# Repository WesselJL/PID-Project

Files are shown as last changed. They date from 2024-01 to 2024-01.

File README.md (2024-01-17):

# PID-Project
PID ball balanceer project 

Het PID bal balanceer project is een project waarbij een balletje wordt gebalanceerd in een goot door middel van een proportioneel-integraal-differentiaal regelaar. De hardware van het project bevat een ESP32 WROOM, VL530IX time of flight sensor en een servo motor. Deze elektro componenten zijn geinstalleerd op een 3D geprinte opstelling die ontworpen is (zie afbeelding van de opstelling hieronder).

WhatsApp Image 2024-01-15 at 14 33 00

## **Uitleg ontwerpkeuzes 3D print**

Het ontwerp van de 3D modellen is zo simpel mogelijk gemaakt. Het gehele model is opgedeeld in 4 delen zodat het op elke gemiddelde 3D printer geprint kan worden en zodat wanneer een onderdeel vervangen of opnieuw ontworpen moet worden het per deel gedaan kan worden. Het ontwerp bestaat uit een goot/ balk waar een balletje in kan rollen. Deze goot/ balk kan in elkaar worden geschoven en wordt bij elkaar gehouden door het middelste kantelpunt waar een bout door heen zit. Naast het middelste kantelpunt is er nog een ander kantelpunt, dit kantelpunt is het punt waar de servo motor de goot/ balk mee laat bewegen.

Op de 3D geprinte delen zijn bevestigings punten voor zowel de servo motor als de time of flight sensor. Deze motor en sensor zijn vastgemaakt met standaard maat boutjes en moeren. Het vierde en laaste deel van het model is de voetsteun. Deze steun zit vast aan het middelste kantelpunt, het kantelpunt van de servo motor en de servo motor zelf zitten ook vast aan deze voetsteun. 

> [!TIP]
> Zorg er voor dat de bouten van de kantelpunten niet te groot zijn, dit maakt het voor de servo motor moeilijk om te bewegen/ de bal te kantelen.

## **Uitleg Componentkeuze**

Voor dit PID bal balanceer project is er gekozen voor de MG90-servo, de VL53L0X ToF-sensor en de ESP32 WROOM. Deze keuzes zijn gebaseerd op de eigenschappen en functionaliteiten van elk component, deze eigenschappen en functionaliteit zorgen ervoor dat de bal gebalanceerd kan worden door middel van de gecodeerde PID regelaar.

### *MG90 Servo*

MG90S-180-1

De MG90-servo is gekozen vanwege de volgende eigenschappen: nauwkeurig, betrouwbaar, betaalbaar en relatief klein. Met een hoog koppel voor de afmeting van de servo motor en de nauwkeurig stapgrootte maakt de MG90 het moeglijk om de bal precies en snel te balanceren. Bovendien is het compacte formaat van de servo gunstig voor het toepassen in ons project, hierdoor is het te printen onderdeel compact te houden.

### *VL530IX tof sensor*

550x332

De VL53L0X Time-of-Flight-sensor is een belangrijk component in dit project vanwege de mogelijkheid om snel en nauwkeurig afstanden te meten. Het ToF-principe zorgt er voor dat in real-time de afstands gegevens worden verkregen over de afstand tussen de sensor en de bal die gebalanceerd moet worden. Deze gegevens zijn essentieel voor de PID-regeling om snel en effectief te reageren op veranderingen in de positie van de bal. Deze sensor kan afstanden meten tot 2 meter dus dat is ruim voldoende voor deze opstelling. De snelste modus van de sensor kan met een afstand van 1.2 meter en een nauwkeurigheid van +/- 5% elke 20ms een afstand meten. 

### *ESP32 WROOM*

61o2ZUzB4XL _AC_UF894,1000_QL80_

De keuze voor de ESP32 WROOM als microcontroller is gemaakt omdat die een krachtige processor, wifi mogelijkheid en brede ondersteuning in de open source wereld heeft. De dual-core processor op 240 MHz biedt voldoende rekenkracht om de PID-regeling te implementeren en tegelijkertijd andere taken uit te voeren. Bovendien maakt de geïntegreerde Wi-Fi-connectiviteit van de ESP32 WROOM draadloze communicatie mogelijk, waardoor het gemakkelijk is om gegevens PID waardes live aan te kunnnen passen. Dit is een leuke ADD-on voor interactieve lessen voor studenten. 

> [!NOTE]
> De componenten die hierboven genoemd en toegelicht zijn zitten aangesloten op een gaatjes print. De kabels dienen lang genoeg te zijn, dit omdat de sensor met de balk/ goot mee kantelt wanneer de bal gebalanceerd wordt.

## **Uitleg Code**

De code voor dit bal balanceer project d.m.v. PID is gestart door eerst een systeem te maken wat de bal kon balanceren met de sensor waardes die de tof sensor als output gaf zonder PID. Toen de bal succesvol gebalanceerd werd is de PID regeling geprogrammeerd en getest. De uitleg van de 2 programma's en de PID berekeningen staat hieronder.

### *Code zonder PID*

Dit onderstaande gedeelte is het toevoegen van de gebruikte libaries. Zoals de comments het al zeggen zijn het de libaries voor de I2C communicatie, time of flight sensor en de servo motor.

```ruby
#include <Wire.h> // libary voor I2C-communicatie
#include <Adafruit_VL53L0X.h> // VL53L0X sensor libary 
#include <ESP32Servo.h> // libary voor Servo motor
```
Dan als volgende is het de pin initialisatie van de servo motor, initialisatie van de VL53LOX variabele en de servo variabele.

```ruby
#define SERVO_PIN 12 // Definitie van de pin (PIN 12) voor de uitvoer van de aansturing van de Servo-motor
Adafruit_VL53L0X lox = Adafruit_VL53L0X(); // Initialisatie van de sensor variabele
Servo servo; // Initialisatie van de Servo motor
```
In de setup van het programma wordt de seriële communicatie opgesteld en wordt er gecontroleerd of de VL53LOX juist is opgestart. Wanneer dit niet het geval is dan wordt er een foutmelding in de seriële monitor geprint en blijft het systeem in een oneindige 'halt' loop. Daarnaast wordt ook de servo variabele gekoppeld aan de Servo pin en wordt de positie van de servo motor ingesteld op 90 graden, dit is de start positie.

```ruby
void setup() {
  Serial.begin(115200); // Initialisatie van de seriële communicatie met een baudrate van 115200 bps
  Serial.println("Ping Pong Ball Balancing"); // Uitvoer van een start bericht

  if (!lox.begin()) { // Controle op het starten van de VL53L0X-sensor
    Serial.println(F("Failed to boot VL53L0X")); // Uitvoer van een foutmelding bij mislukken en stoppen van het programma
    while (1);
  }

  servo.attach(SERVO_PIN); // Koppeling van de Servo variabele aan de gedefinieerde pin
  servo.write(90); // Instellen van de initiële positie van de Servo-motor op 90 graden

  delay(500); // Wachten om de Servo-motor naar de initiële positie te laten bewegen
}
```
In de loop van het programma wordt de afstand tot de bal gemeten door de sensor en wordt er gecontroleerd of deze meting een geldige meting is. Daarna wordt de de minimale sensor waarde en de maximale waarde omgezet naar een servo waarde van 0 tot 180. Dit wordt gedaan met de "map" functie. Vervolgens wordt de variabele "servoPosition" naar de Servo gestuurd. In de volgende [video](https://youtu.be/PQ2CX1DTkAU) kan je zien hoe de bal gebalanceerd wordt zonder PID, 

```ruby
void loop() {
  VL53L0X_RangingMeasurementData_t measure; // Definitie van de bal voor de VL53L0X-sensor
  
  lox.rangingTest(&measure, false); // Uitvoeren van een afstandsmeting met de VL53L0X-sensor

  if (measure.RangeStatus != 4) {  // Controleren of de meting geldig is
    int distance = measure.RangeMilliMeter; // Uitlezen van de gemeten afstand in millimeters
    Serial.print("Distance (mm): "); // Uitvoer van het label "Distance (mm): "
    Serial.println(distance); // Uitvoer van de gemeten afstand
    
    // Aanpassen van de positie van de Servo-motor op basis van de gemeten afstand
    int servoPosition = map(distance, 20, 270, 0, 180); // Aanpassen van de mapping-bereik op basis van de opstelling
    servo.write(servoPosition); // Aansturen van de Servo-motor naar de berekende positie
    
    delay(50); // Aanpassen van deze vertraging om de responsiviteit van het systeem te regelen
  } else {
    Serial.println("Out of range"); // Uitvoer van een melding wanneer de gemeten afstand buiten bereik is
  }
}
```
> [!IMPORTANT]
> De waardes 20 & 270 in de 'int servoPosition = map(distance, 20, 270, 0, 180);' line moeten worden aangepast naar de minimale en maximale sensor waarde van je eigen sensor. Deze zijn te verkrijgen door je object wat gebalanceerd moet worden op zijn positie die het dichtsbij de sensor zit en het verste weg van de sensor zit. Deze zijn uit te lezen door het uitvoeren van onderstaande code:

```ruby
#include <Wire.h> // libary voor I2C-communicatie
#include <Adafruit_VL53L0X.h> // libary voor VL53L0X sensor

Adafruit_VL53L0X lox = Adafruit_VL53L0X(); // Initialisatie van de VL53L0X variabele

void setup() {
  Serial.begin(115200); // Initialisatie van de seriële communicatie met een baudrate van 115200 bps
  Serial.println("Ping Pong Ball Balancing"); // Uitvoer van een begroetingsbericht

  if (!lox.begin()) { // Controle op het starten van de VL53L0X-sensor
    Serial.println(F("Failed to boot VL53L0X")); // Uitvoer van een foutmelding bij mislukken en stoppen van het programma
    while (1);
  }

  delay(500); // Wachten om de sensor op te starten
}

void loop() {
  VL53L0X_RangingMeasurementData_t measure; // Definitie van de bal voor de VL53L0X-sensor
  
  lox.rangingTest(&measure, false); // Uitvoeren van een afstandsmeting met de VL53L0X-sensor

  if (measure.RangeStatus != 4) {  // Controleren of de meting geldig is
    int distance = measure.RangeMilliMeter; // Uitlezen van de gemeten afstand in millimeters
    Serial.print("Distance (mm): "); // Uitvoer van het label "Distance (mm): "
    Serial.println(distance); // Uitvoer van de gemeten afstand
    
    delay(50); // Aanpassen van deze vertraging om de responsiviteit van het systeem te regelen
  } else {
    Serial.println("Out of range"); // Uitvoer van een melding wanneer de gemeten afstand buiten bereik is
  }
}
```

### *PID berekening*

Een volledige PID output kan beschreven worden door de volgende formule:

$$ u(t) = K_p e(t) + K_i \int_{0}^{t} e(\tau) d\tau + K_d \frac{de(t)}{dt} $$ 

$u(t)$ : Dit is de output van de berekening

$e(t)$ : Dit is de error die zich nog in de output bevindt ten opzichte van het setpoint

$K_p$ : Dit is de proportionele factor van het systeem

$K_i$ : Dit is de integrale factor van het systeem

$K_d$ : Dit is de afgeleide factor van het systeem

Deze formule berekent op basis van de fout tussen het gewenste punt en de huidige meetwaarde een output die bijvoorbeeld de aansturing van een motor, de positie van een servo of de tempratuur in je huis aan geeft. $e(t)$ is de fout op een bepaald moment in de tijd en het verschil tussen de waarde waar je wilt eindigen en de werkelijke waarde op dat moment. $K_p$ is de proportionele factor van het systeem, deze waarde bepaalt hoe sterk de uitvoer reageert op de directe fout. $K_i$ is de integrale factor. Deze factor neemt de afwijkingen uit het verleden en telt de waardes op en corrigeert daarmee binnen I-tijd (in seconden) de aansturing/ output waarde. $K_d$ Dit is de afgeleide factor van het systeem en meet de snelheid waarmee de fout veranderd. Dit zorgt er voor dat overshoot wordt verminderd (het voorbij de vooraf ingestelde waarde/ setpoint gaan). Voor meer uitgebreide informatie en voorbeelden van PID systemen zie deze [link](https://nl.wikipedia.org/wiki/PID-regelaar) naar de uitleg.

### *Code met PID*

In de code voor het balanceren van de bal met een PID regeling worden er een aantal variabelen in de code toegevoegd. Deze variabelen zijn de huidige tijd en de laatste tijd, de waardes voor P, I en D en de error die het systeem heeft. Daarnaast is er ook nog een variabele om de tijd in op te slaan tussen de metingen en een variabele voor de vorige foutwaarde.

```ruby
double sensorValue; // Variabele voor het opslaan van de gelezen sensorwaarde
double currentTime; // Huidige tijdvariabele voor het regelen van de meetfrequentie
double lastTime; // Variabele voor het opslaan van de laatste tijd
double P = 2; // Proportionele term voor de PID-regelaar
double I = 0.1; // Integratieve term voor de PID-regelaar
double D = 0.1; // Differentiërende term voor de PID-regelaar
double error; // Variabele voor het opslaan van de fout in de regeling
double dt; // Tijd tussen metingen voor de PID-regelaar
double setpoint = 550; // Gewenste sensorwaarde
double previous; // Vorige foutwaarde voor de differentiërende term in de PID-regelaar
```
De code in de setup blijft het zelfde. De seriële communicatie wordt nog steeds geïnitialiseerd en de servo positie wordt weer naar een "start" waarde gezet.  

> [!WARNING]
> De goeie waardes voor P, I en D om een stabiel systeem te krijgen verschillen voor elke opstelling. Door middel van trial en error zijn de waardes voor een verschillend systeem vinden (denk aan een zwaardere bal of dergelijk).

De functie 'calculatePID' berekend de juiste output om de servo aan te sturen en returnt deze. 

*Proportioneel*: De fout 'error' wordt vermenigvuldigd met de proportionele factor 'P'.

*Integraal*: De fout 'error' wordt vermenigvuldigd met de *dt* sampletijd, de vorige berekende waarde van de integraal wordt hierbij opgeteld. Vervolgens wordt dit nog vermenigvuldigd met de integrale factor 'I'.

*Differentiaal*: De fout 'error' wordt afgetrokken van de vorige fout en gedeeld door de *dt* sampletijd. Deze uitkomst wordt vermenigvuldigd met de differentiale factor 'D'.

Uiteindelijk geeft de functie de opgetelde som van deze drie waardes, dus Proportioneel + Integraal + Differentiaal.

```ruby
double calculatePID() {
  double proportioneel = error * P; // Bereken de proportionele term
  double integraal = (integraal + error * dt) * I; // Bereken de integratieve term
  double differentiaal = ((error - previous) / dt) * D; // Bereken de differentiërende term
  previous = error; // Bijwerken van de vorige foutwaarde
  return (proportioneel + integraal + differentiaal); // Bereken de totale PID-uitvoer
}
```
De loop in deze code ziet er als volgt uit: 

```ruby
void loop() {
  if (millis() - currentTime >= 50) { // Regel de meetfrequentie
    currentTime = millis();
    double now = millis();
    dt = (now - lastTime) / 1000.0; // Bereken de tijd tussen metingen
    lastTime = now;

    sensorValue = readSensor(); // Lees de sensorwaarde
    sensorValue = map(sensorValue, 20.0, 350.0, 0.0, 1000.0); // Mapping van de sensorwaarde naar een specifiek bereik
    error = setpoint - sensorValue; // Bereken de fout in de regeling
    double output = calculatePID(); // Bereken de PID-uitvoer

    output = map(output, -1000, 1000, 210, 60); // Mapping van de PID-uitvoer naar een geschikt bereik

    // Begrens de servo-uitvoer binnen bepaalde grenzen zodat de servo niet extreme waardes binnen krijgt wanneer er een PID waarde tussen zit die extreem anders is dan de gemiddelde waarde, hierdoor blijft de servo binnen de gestelde waardes van 60 en 220
    if (output < 60) {
      output = 60;
    }
    if (output > 220) {
      output = 220;
    }

    myServo.write(output); // Stuur de Servo-motor aan naar de berekende positie

    Serial.println(output); // Uitvoer van de PID-uitvoer
    Serial.println(sensorValue); // Uitvoer van de gemeten sensorwaarde
  }
}
```
De loop begint met een if statement die ervoor zorgt dat het programma in de 'if' elke 50ms wordt uitgevoerd. 50ms is gekozen omdat de servo niet sneller kan reageren.

Vervolgens wordt de exacte $d(t)$ berekend die tussen de cycles in zit, dit is nodig om precies de Integraal en Differentiaal te kunnen regelen. 

Daaronder wordt de Sensor uitgelezen, gemapt naar 0 tot 1000, de error berekend en de calculatePID berekening aangeroepen. 

Uiteindelijk wordt de output gemapt naar een geschikt bereik voor de servo. 210 is de meest lage stand en 60 is de meest hoge stand.

Met *myServo.write(output);* wordt de servo nog geüpdate. 

De code met PID kan je zien in de volgende [video](https://youtu.be/Alv6lQySq_s)

### *Code voor het veranderen van PID waardes in web interface* 

Om de PID waardes te veranderen in een web interface wordt er in de setup van de code een deel toegevoegd wat er voor zorgt dat de ESP32 wordt geconfigureerd als acces point. Vervolgens geeft de code een ip address die gebruikt kan worden om naar de web interface te navigeren. De code hiervan staat hieronder uitgelegd:

```ruby
  // Verbind met het Wi-Fi-netwerk met SSID en wachtwoord
  Serial.print("Setting AP (Access Point)…");
  // Verwijder het wachtwoordparameter als je wilt dat het AP (Access Point) open is
  WiFi.softAP(ssid, password);

  IPAddress IP = WiFi.softAPIP();
  Serial.print("AP IP address: ");
  Serial.println(IP);

  server.begin();
```
In de void executeWiFi worden een heel aantal dingen gedaan en hieronder worden de belangrijkste dingen toegelicht:

om de HTML webpagina te tonen met 3 invoer velden van de PID waardes en 3 bevestigings knoppen wordt de volgende code gebruikt
```ruby
            // Toon de HTML-webpagina
            client.println("<!DOCTYPE html><html>");
            client.println("<head>");
            client.println("<meta name=\"viewport\" content=\"width=device-width, initial-scale=1\">");
            client.println("</head>");
            client.println("<body>");

            // Werk de formulieractie bij om de POST-methode te gebruiken
            client.println("<form action=\"/update\" method=\"post\">");

            // Werk de waarde van de tekstvelden bij met de huidige waarden van P, I en D
            client.println("<p>P: <input type=\"text\" name=\"P\" class=\"text-field\" pattern=\"[+-]?([0-9]*[.])?[0-9]+\" value=\"" + String(P) + "\"></p>");
            client.println("<p>I: <input type=\"text\" name=\"I\" class=\"text-field\" pattern=\"[+-]?([0-9]*[.])?[0-9]+\" value=\"" + String(I) + "\"></p>");
            client.println("<p>D: <input type=\"text\" name=\"D\" class=\"text-field\" pattern=\"[+-]?([0-9]*[.])?[0-9]+\" value=\"" + String(D) + "\"></p>");

            // Voeg een verzendknop toe voor elke variabele om de formulierinzending te activeren
            client.println("<p><input type=\"submit\" name=\"updateP\" value=\"Update Values\"></p>");
```
Hierin worden de de PID waardes bijgewerkt op basis van de input, daarnaast zorgt dit deel ook voor de layout van de webpagina. Nadat er waardes zijn ingevuld voor P, I en D worden de waardes verstuurd naar de variabelen die eerder zijn uitgelegd. Dit wordt gedaan met de volgende regels code:

```ruby
// Werk de PID-parameter bij op basis van de POST-gegevens
void updateParameter(String postBody, String paramName, float &param) {
  int paramIndex = postBody.indexOf(paramName + "=");
  if (paramIndex != -1) {
    String paramValue = postBody.substring(paramIndex + paramName.length() + 1);
    param = paramValue.toFloat(); // Zet de string om naar een float en werk de parameter bij
    Serial.print("Updated " + paramName + ": ");
    Serial.println(param);
  }
}
```

Wanneer de codes die in de bestanden staan worden overgenomen en de juiste libaries zijn toegevoegd dan zou het systeem moeten werken zoals te zien is in de video's. Verannder de P, I en D waardes om de verschillende responsies van het systeem te kunnen zien.

---------------------------------------------------------------------------------------------------------------------------------------------------------------------------------------------------

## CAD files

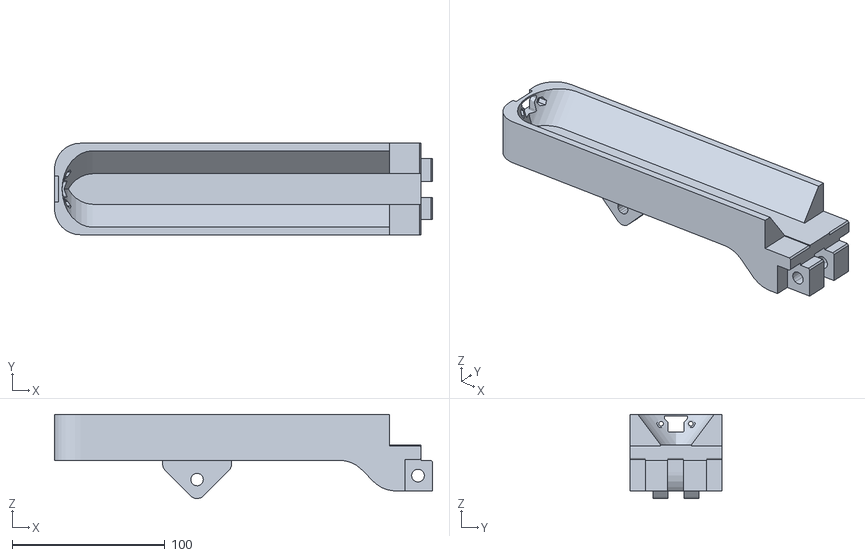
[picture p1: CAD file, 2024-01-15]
STL bestanden 3D ontwerp/P2.2.stl
247.5 x 60.0 x 55.0

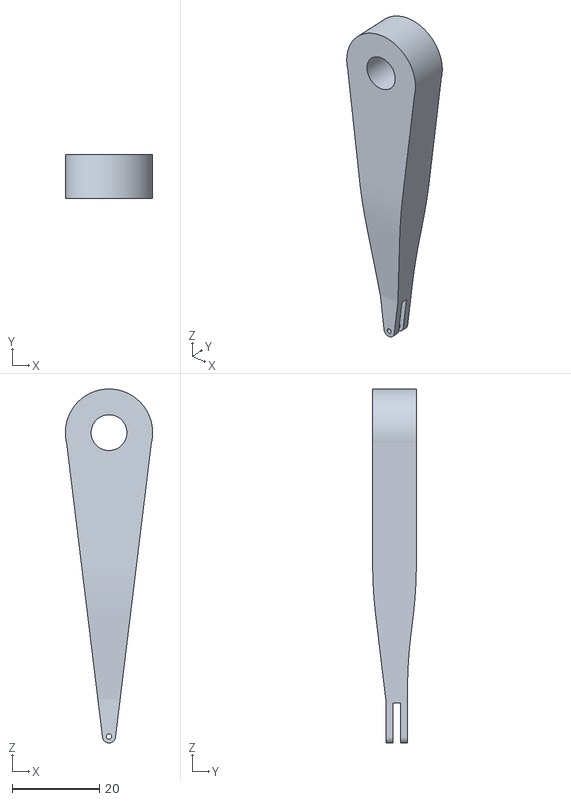
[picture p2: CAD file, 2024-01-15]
STL bestanden 3D ontwerp/P4.stl
20.0 x 10.0 x 81.1

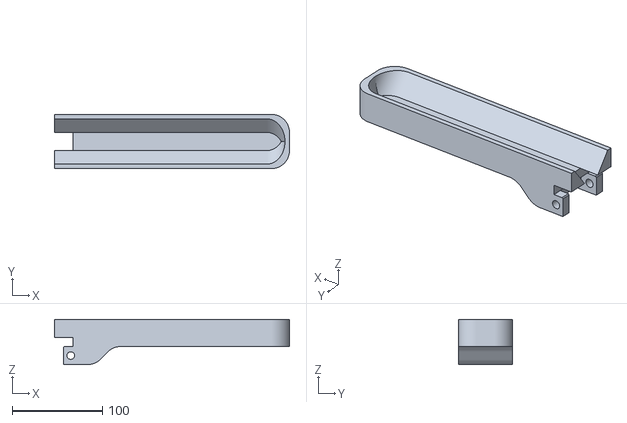
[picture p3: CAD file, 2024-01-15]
STL bestanden 3D ontwerp/P1.stl
260.0 x 60.0 x 50.0

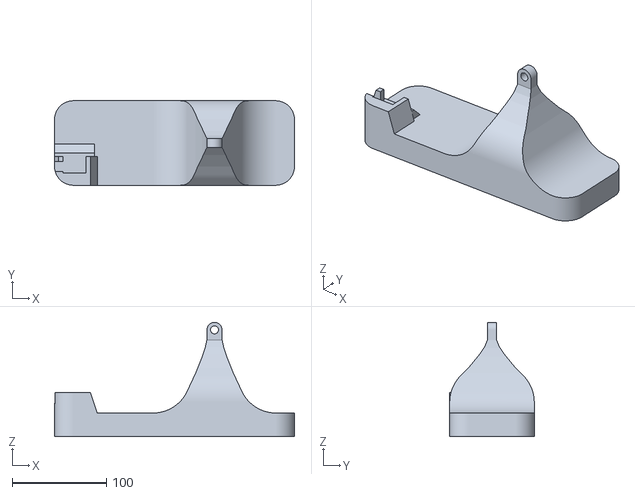
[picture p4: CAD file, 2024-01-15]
STL bestanden 3D ontwerp/P3.stl
254.1 x 89.5 x 121.0

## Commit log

2024-01-15 Create Code zonder PID
2024-01-15 Create Code **met** PID
2024-01-15 Rename Code **met** PID to Code met PID
